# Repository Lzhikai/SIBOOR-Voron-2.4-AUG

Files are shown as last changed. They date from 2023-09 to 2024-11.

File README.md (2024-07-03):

# SIBOOR-Voron-2.4-AUG  

[1. Assembly Manual 2.4r2](#1-assembly-manual-24r2)  
 
[2. Leveling plan](#2-tap-assembly-tutorial)  
 - [TAP Assembly Tutorial](#2-tap-assembly-tutorial)
 - [Cartographer3d official website](https://docs.cartographer3d.com)
 - [Cartographer3d Assembly Tutorial](#3-cartographer3d-assembly-tutorial)  
    ---(Printed version)---  
    ---(CNC version)---  

[3. Stealthburner Assembly Tutorial](#4-stealthburner-assembly-tutorial)  
 - [Y-axis limit](#install-the-y-axis-limit-switch)  
 - [Display assembly](#display-assembly)

[4. Wiring and Inspection](#4-wiring-and-inspection)  

[5. Nevermore Installation](#5-nevermore-installation)  

[6. Networking and Configuration](#6-networking-and-configuration)  
 - [Connect to WiFi](#connect-to-wifi)
 - [SSH Tools PUTTY](#ssh-tools-putty)

[7. Connect the motherboard and EBB CAN Board](#connect-the-octopus-pro-mainboard)  

 - [Connect the Octopus Pro Mainboard](#connect-the-octopus-pro-mainboard)  

 - [Connect the EBB CAN Board](#connect-the-ebb-can-board)  

[FAQ](#faq)  

## Assembly Guide
### VORON 2.4, designed by VORON DESIGN, represents an enhanced CoreXY design featuring a stable bed and a gantry that moves vertically along the Z-axis. Notably, this design introduces added complexity, incorporating features like 4-point gantry tramming for precise alignment with the print surface, additional stepper motors, and other unique elements. Furthermore, it is crafted to operate within a fully enclosed environment, making it exceptionally proficient in printing ABS or similar filaments.
### Thank you for purchasing the V2.4 [AUG] 3D printer kit from SIBOOR. Due to version differences, please carefully read the following steps. If you encounter any issues or difficulties, please contact us promptly. Wishing you a smooth experience ahead.
### Join our Discord and WeChat groups to receive after-sales support.

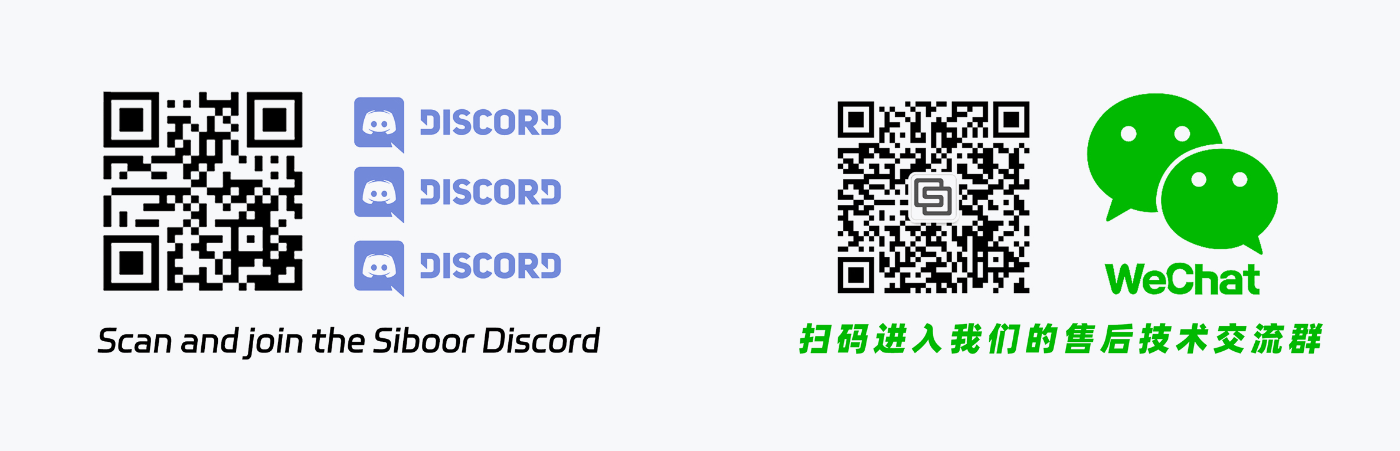
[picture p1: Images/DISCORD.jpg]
 <br/><br/>  

### Please read in the order presented on this page.

### 1. Assembly Manual 2.4r2

- [Assembly_Manual 2.4r2 SIBOOR Annotation Version.pdf](https://github.com/Lzhikai/SIBOOR-Voron-2.4-AUG/blob/main/Manual/Assembly_Manual_2.4r2%EF%BC%88SIBOOR%20Annotation%20Version%EF%BC%89.pdf)  
- Pay close attention to manual comments. After downloading, open the file using a browser or PDF software to view the annotation content!  
- Green-highlighted sections denote variances between SIBOOR V2.4 [AUG] and VORON's official BOM.  
- Red-highlighted sections indicate differences in metal structural components between SIBOOR V2.4 [AUG] and VORON's official BOM.  
  
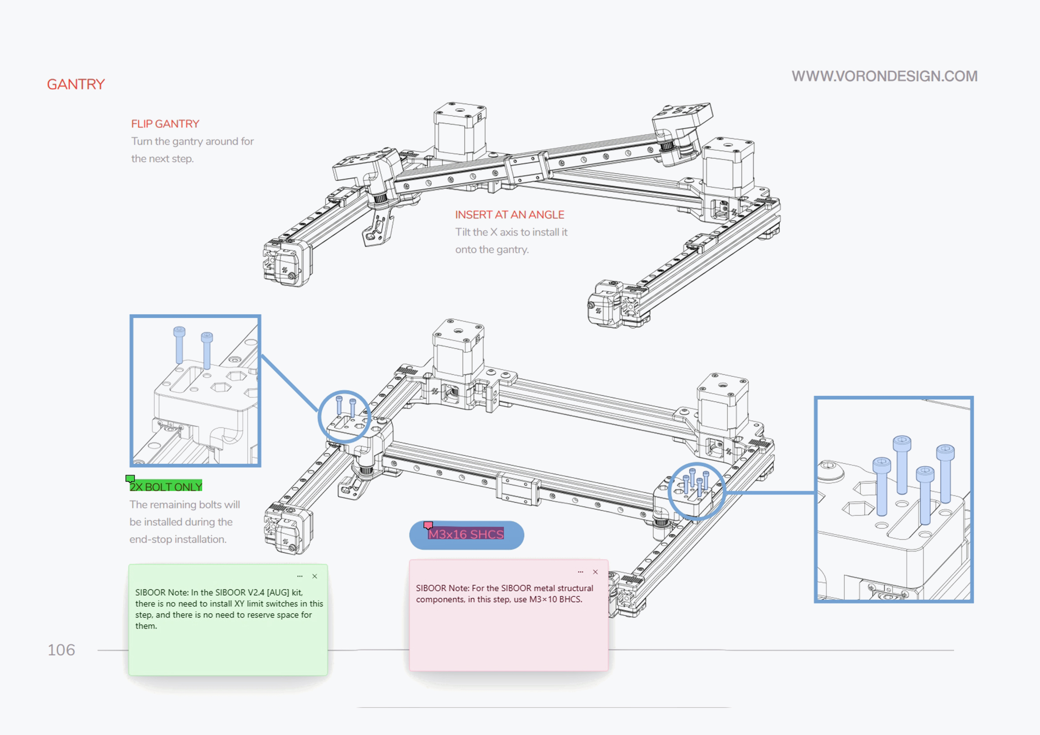
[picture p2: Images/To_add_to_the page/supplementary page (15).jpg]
  

### 2. TAP Assembly Tutorial  

- [Assembly_Manual_Tap.pdf](https://github.com/Lzhikai/SIBOOR-Voron-2.4-AUG/blob/main/Manual/Assembly_Manual_Tap.pdf)  

- Currently, TAP has been upgraded to the RCB version. See the differences in assembly with the old version in the following images.  
  
- **Belt handling:**
  The belts are now handled by looping around Tap_center, and secured with a printed belt cover and M3x8 BHCS:  
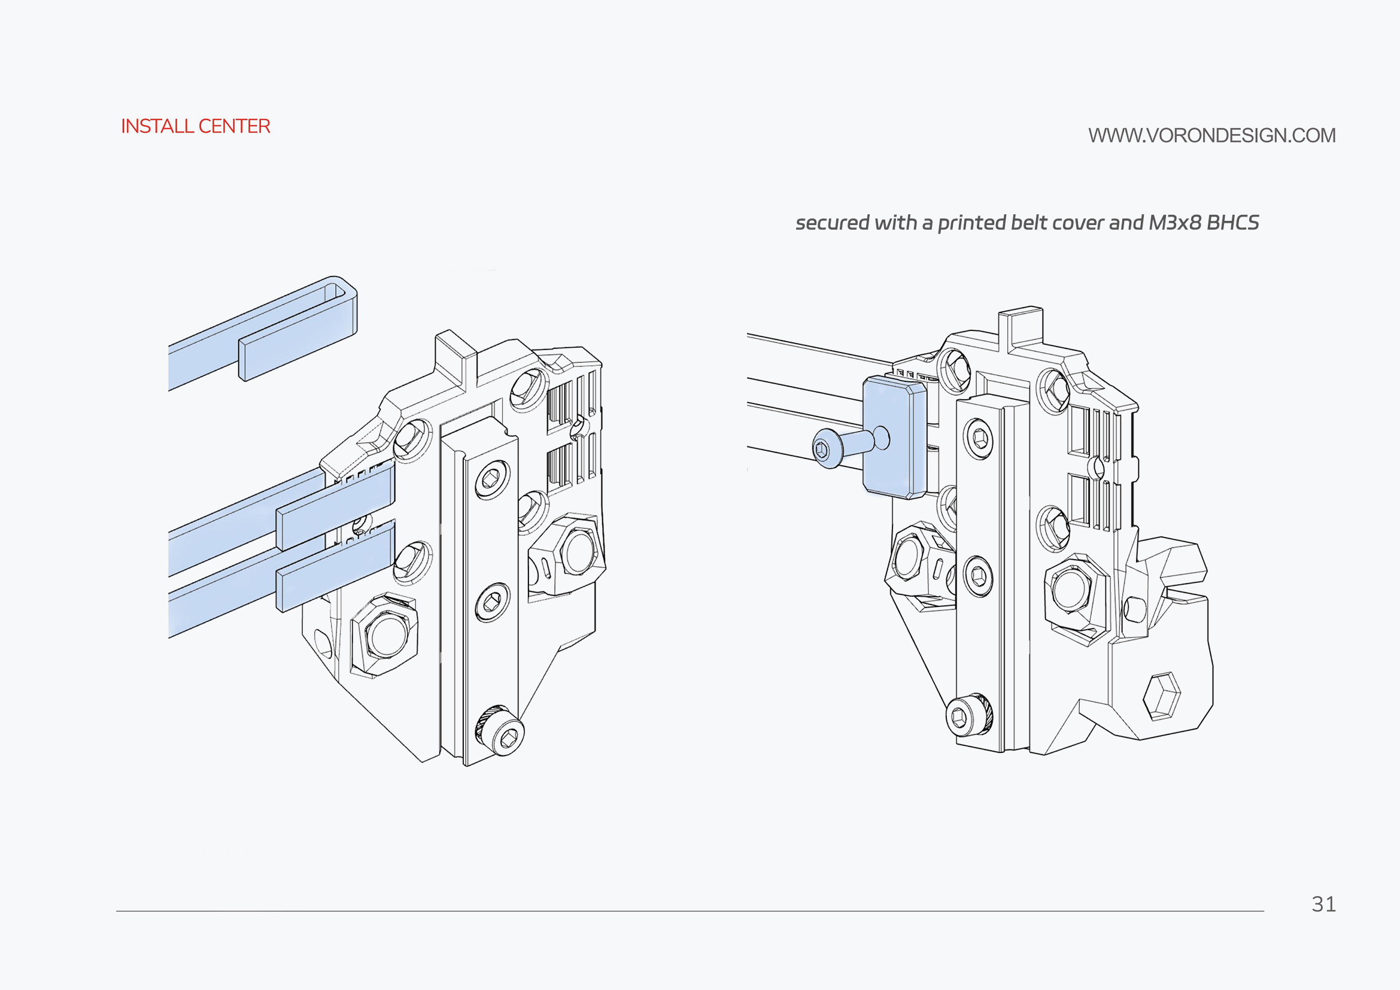
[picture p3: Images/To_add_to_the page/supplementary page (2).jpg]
    

- **Extra Stiffening:**
  The 2 M3x50 bolts are threaded up into Tap_Center, and serve to provide extra stiffening:  
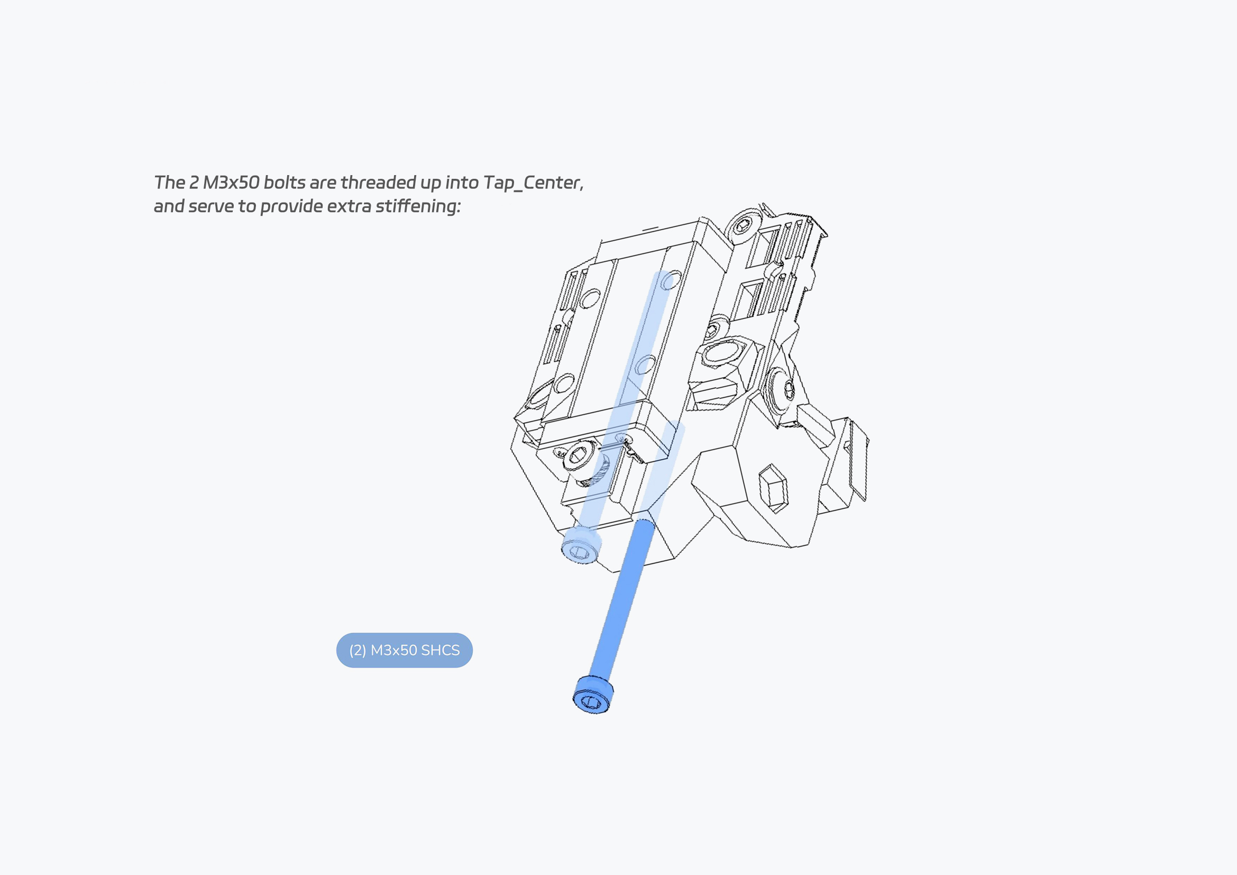
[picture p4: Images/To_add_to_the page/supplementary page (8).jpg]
    

- **Vibration Resistance:**
  The heatset inserts for the center are moved back 4 mm to provide extra vibration resistance:  
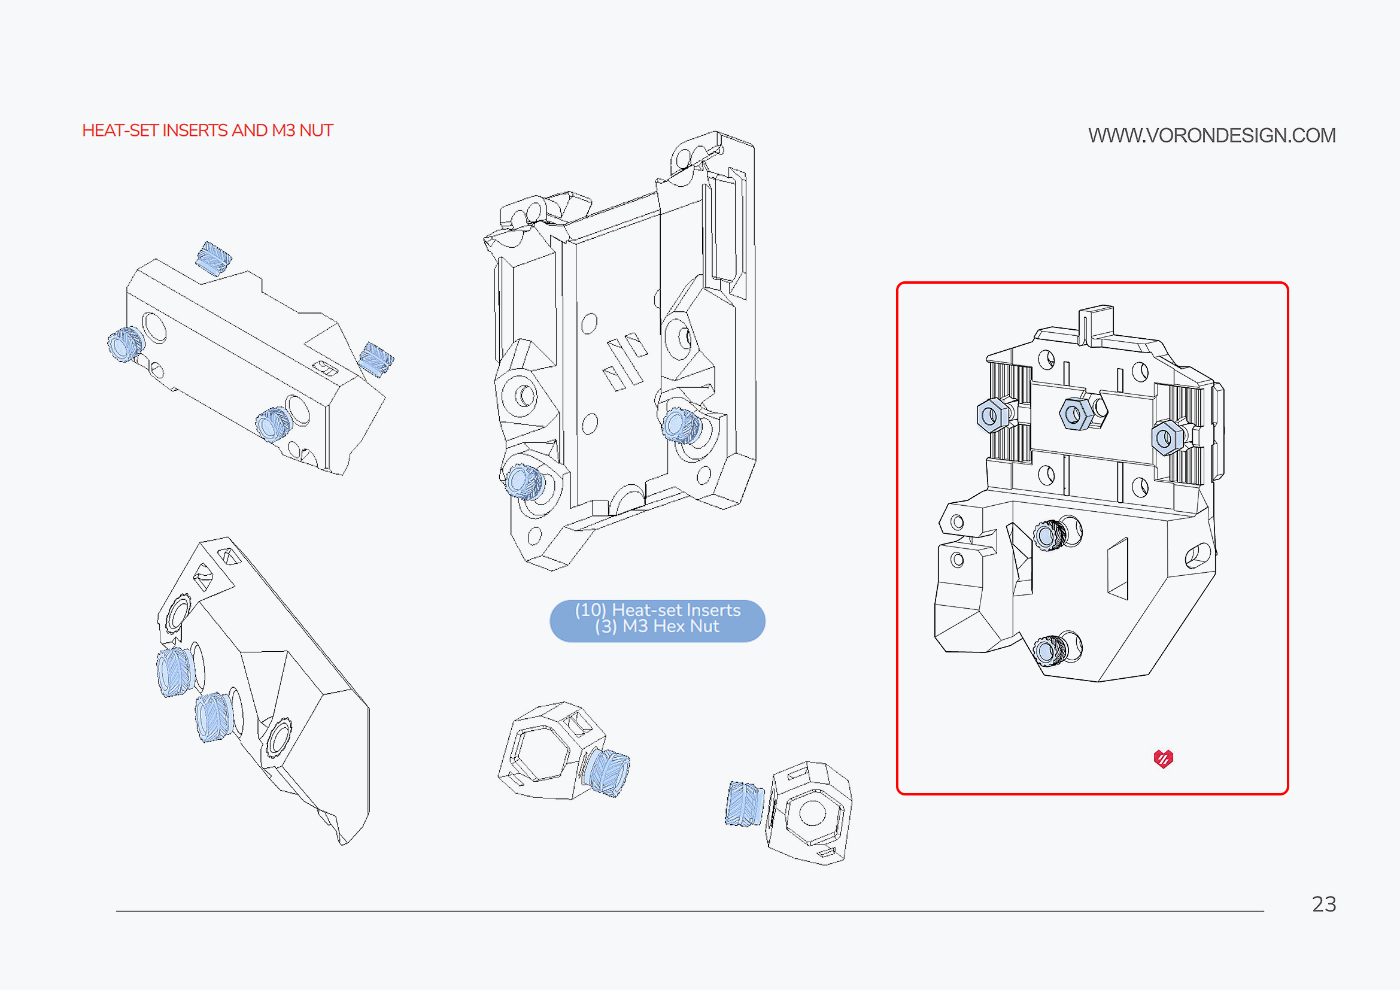
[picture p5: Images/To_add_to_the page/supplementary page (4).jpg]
    

- **Secure with Screws:**
  So they will need to be secured with M3x12 and M3x16 SHCS (The top is still secured by M3x6 SHCS):  
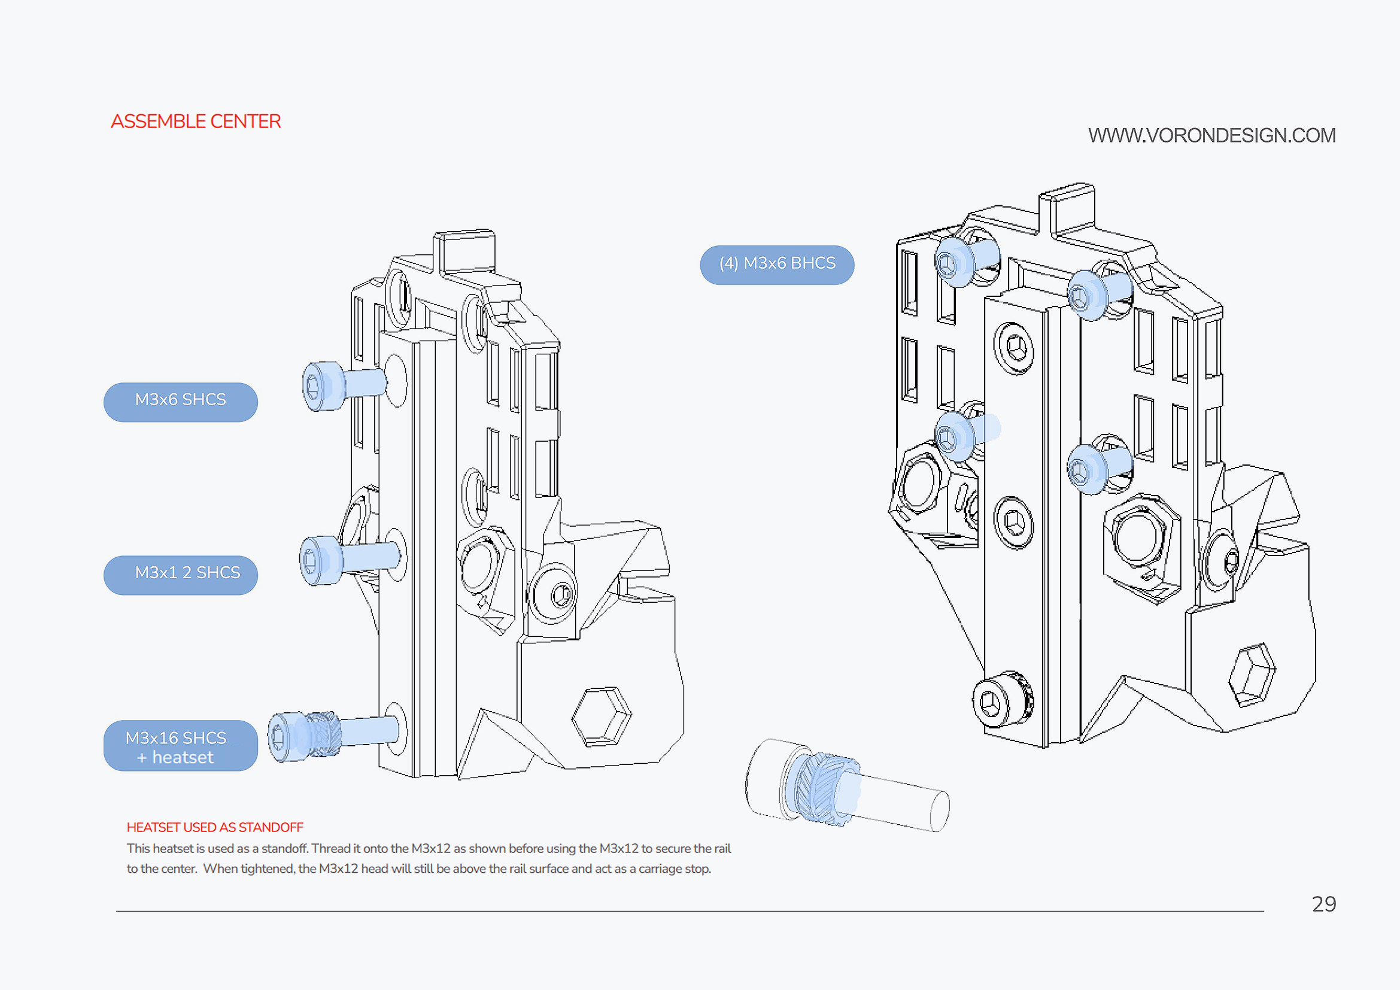
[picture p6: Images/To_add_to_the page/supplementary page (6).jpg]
    

- After completing the TAP module, go directly to page 132 of the "Assembly_Manual 2.4r2 SIBOOR Annotation Version.pdf.  

### 3. Cartographer3d Assembly Tutorial  
- ### Printed version
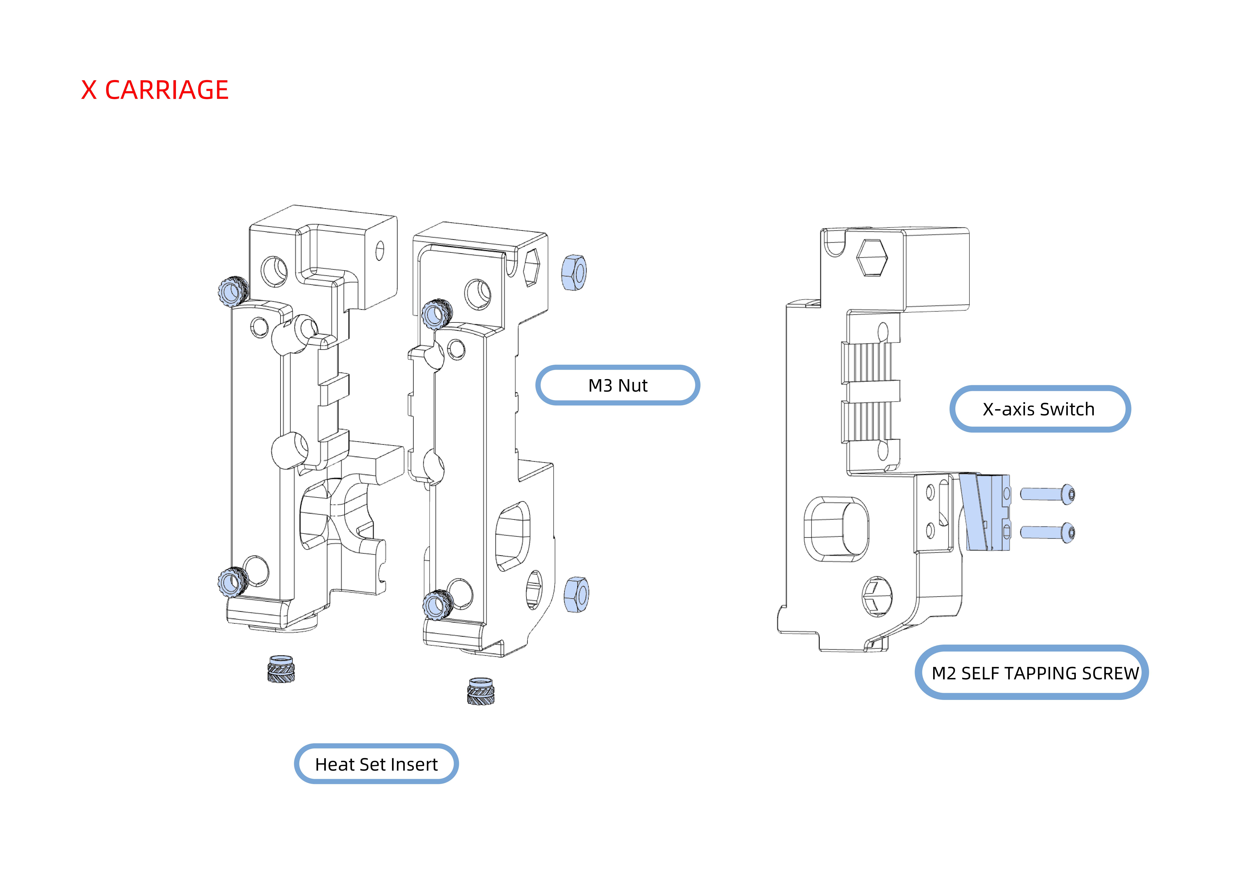
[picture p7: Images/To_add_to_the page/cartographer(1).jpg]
    
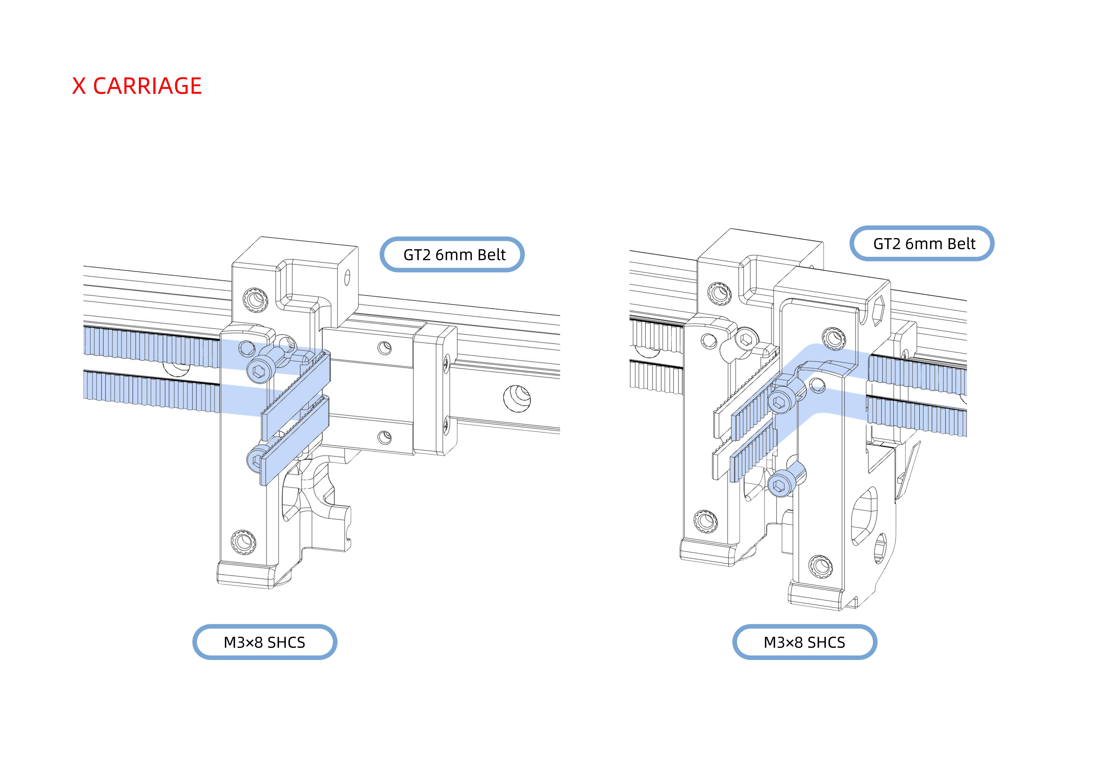
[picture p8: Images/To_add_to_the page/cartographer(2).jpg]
    
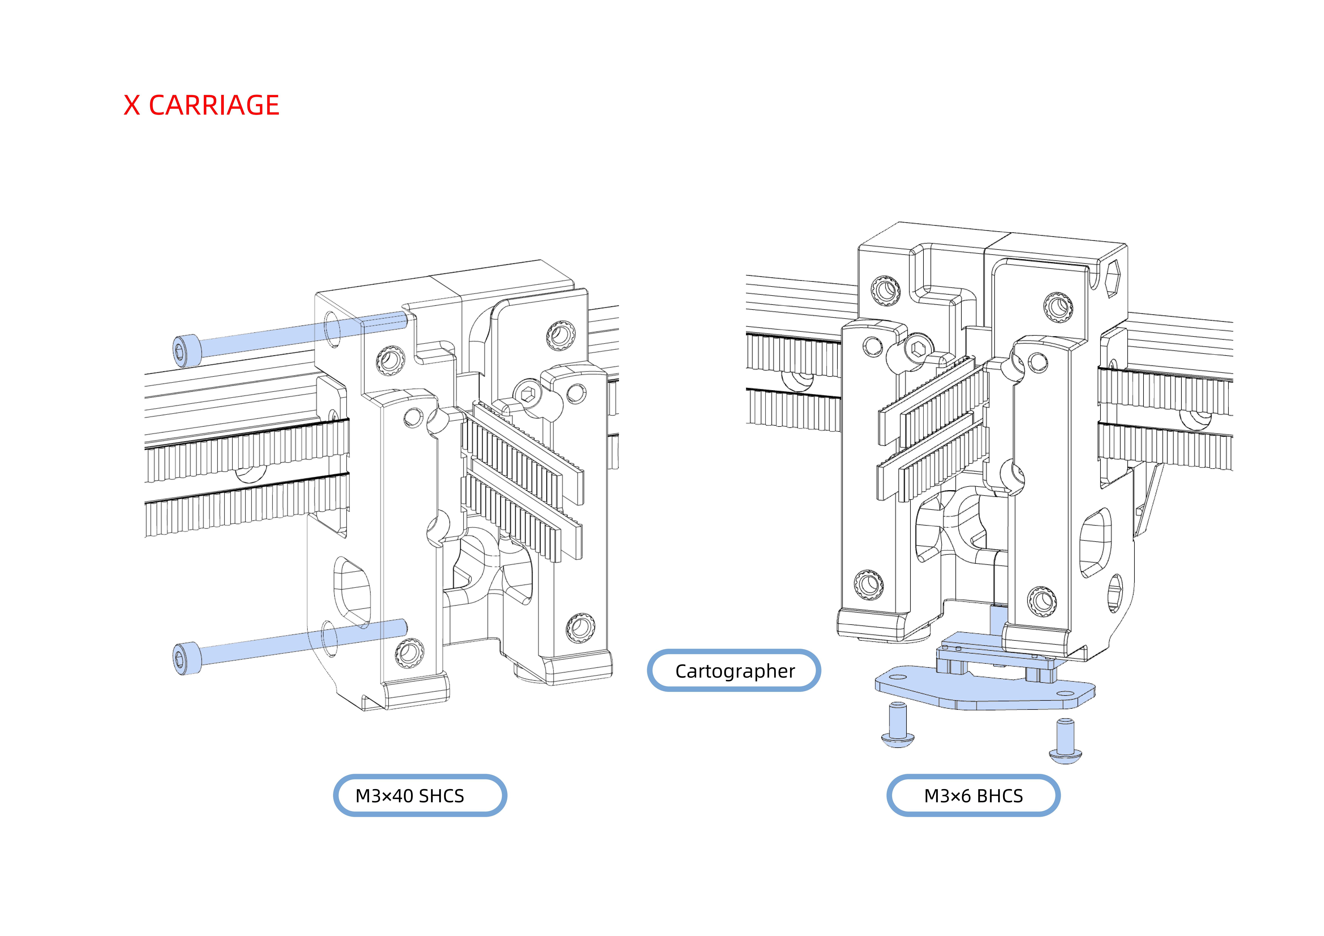
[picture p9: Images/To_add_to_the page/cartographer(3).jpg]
  
- ### CNC version
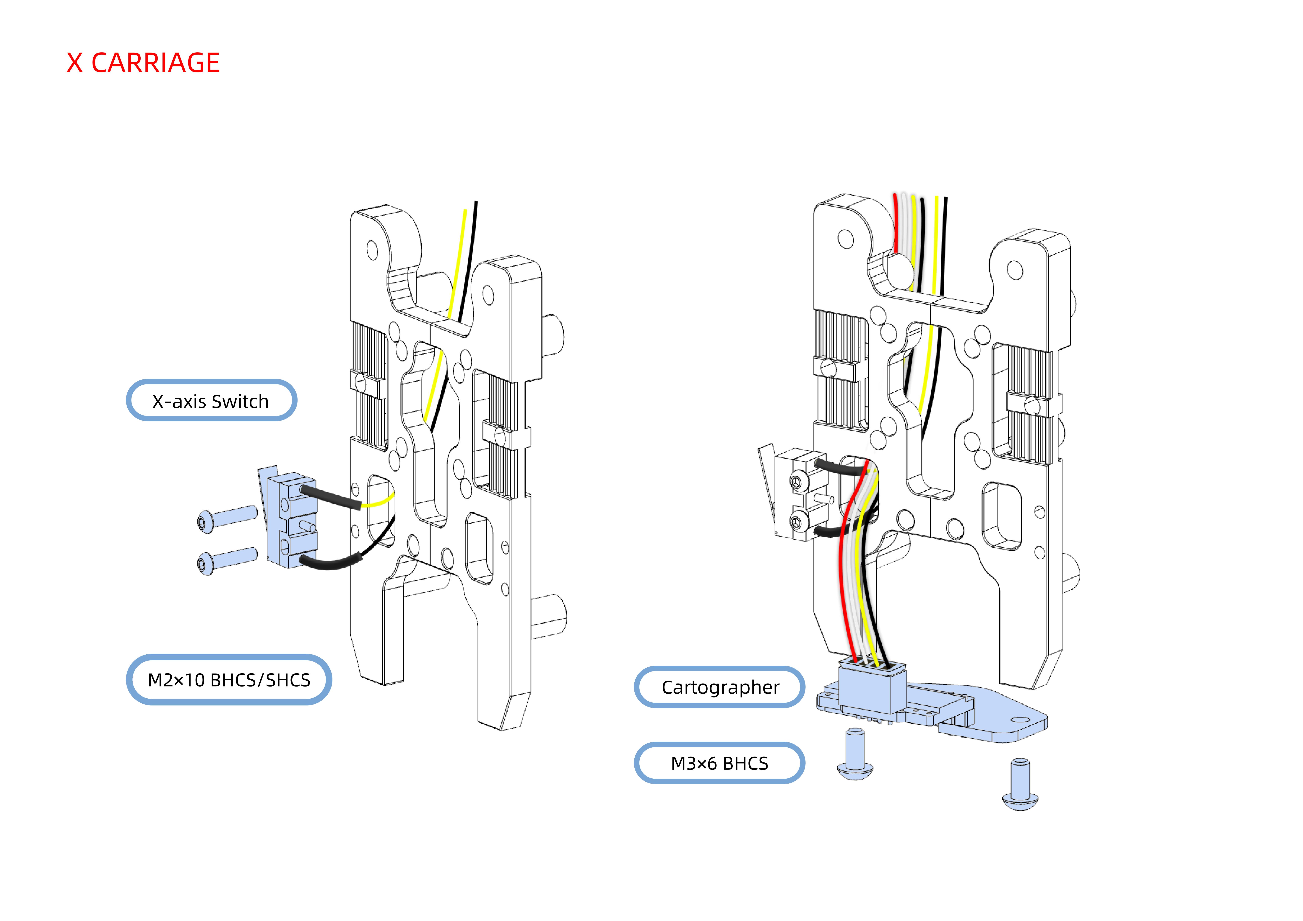
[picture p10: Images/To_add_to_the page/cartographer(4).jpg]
    
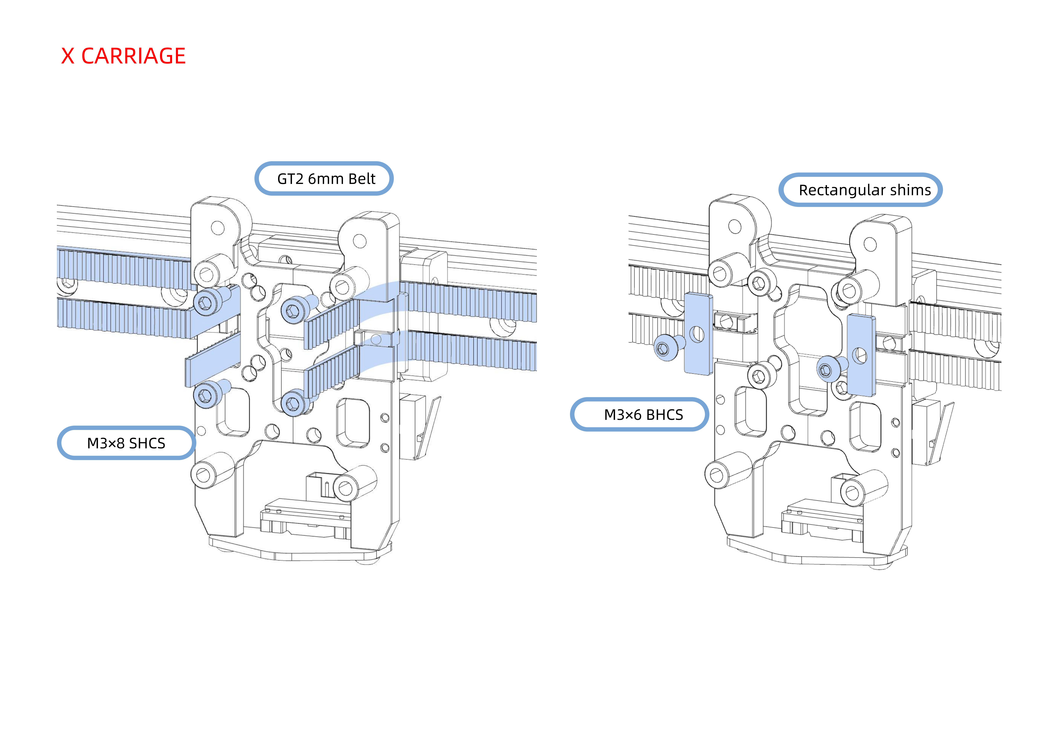
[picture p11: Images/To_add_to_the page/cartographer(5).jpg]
    
  
### 4. Stealthburner Assembly Tutorial  

- Install the heating rod and thermistor.  
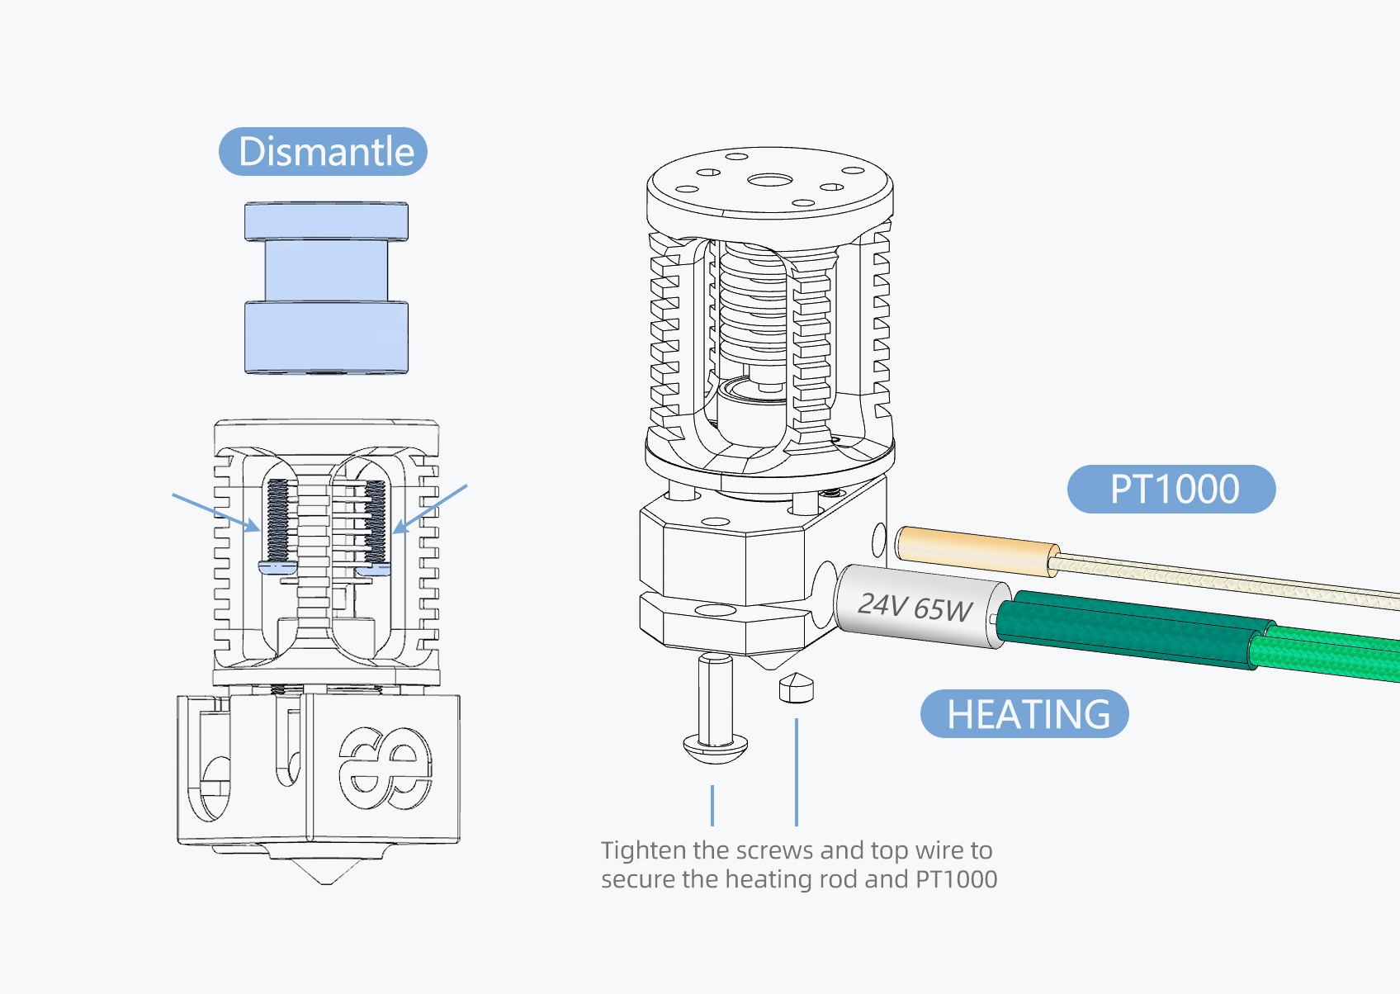
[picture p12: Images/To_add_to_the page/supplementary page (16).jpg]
    

- [Assembly_Manual_Stealthburner.pdf](https://github.com/Lzhikai/SIBOOR-Voron-2.4-AUG/blob/main/Manual/Assembly_Manual_SB%EF%BC%88SIBOOR%20Annotation%20Version%EF%BC%89.pdf)  

- Set up the CAN board, illustrate wiring, and set jumpers.  
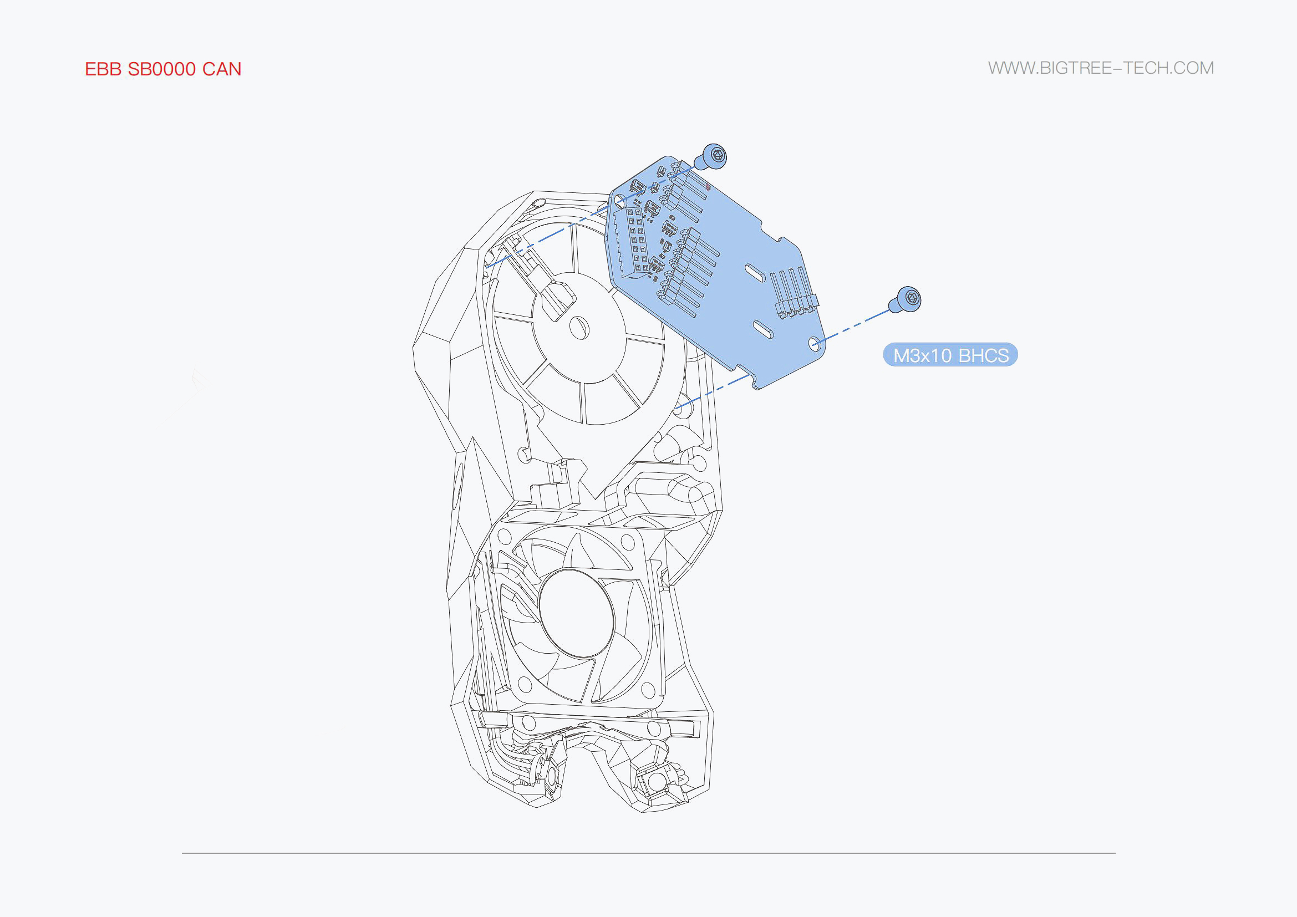
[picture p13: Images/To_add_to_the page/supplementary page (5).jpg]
    
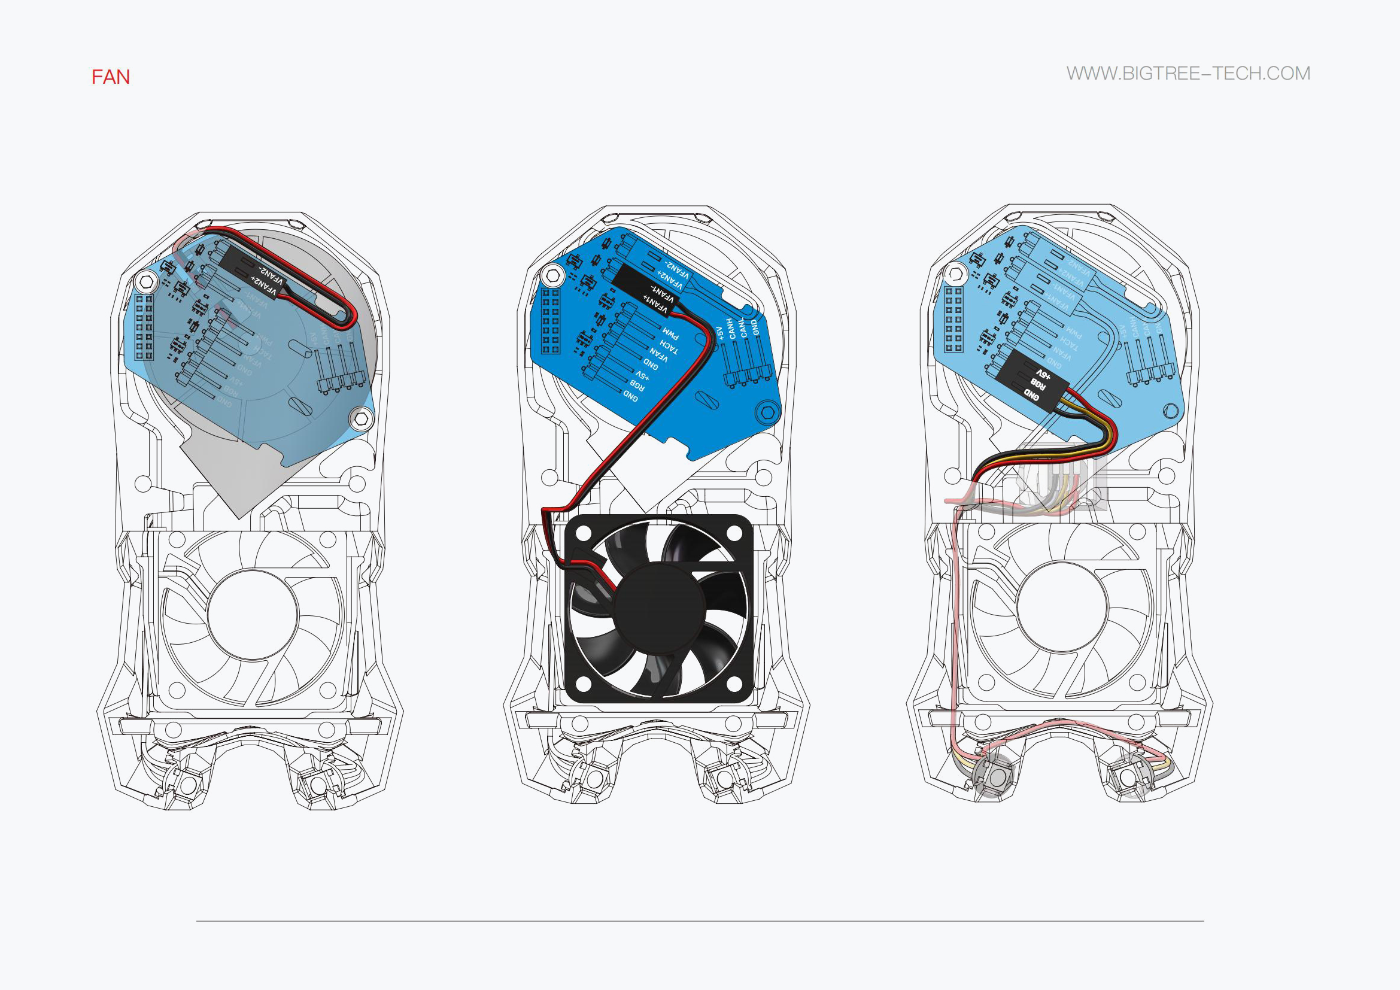
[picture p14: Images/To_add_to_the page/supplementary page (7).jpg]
    
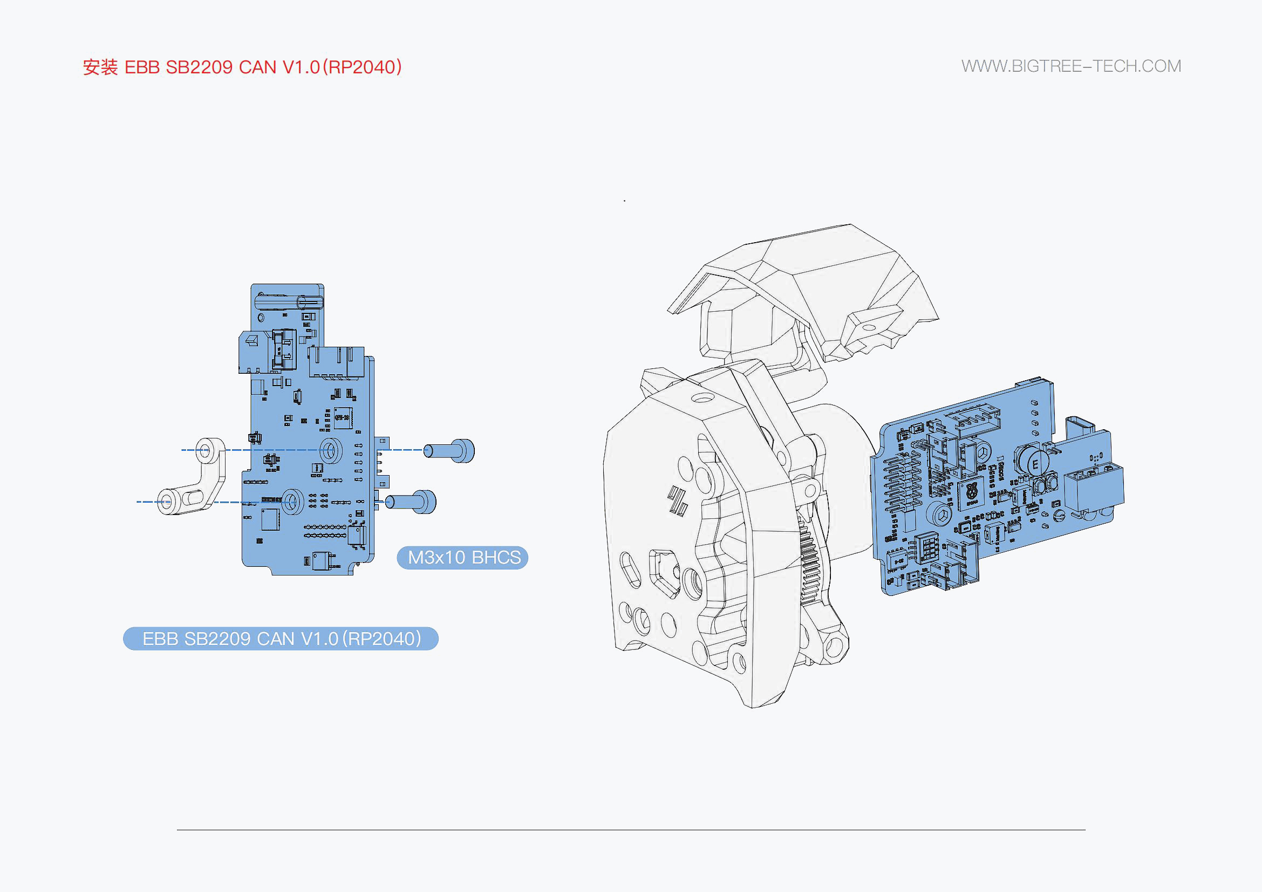
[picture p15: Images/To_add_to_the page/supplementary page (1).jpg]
    
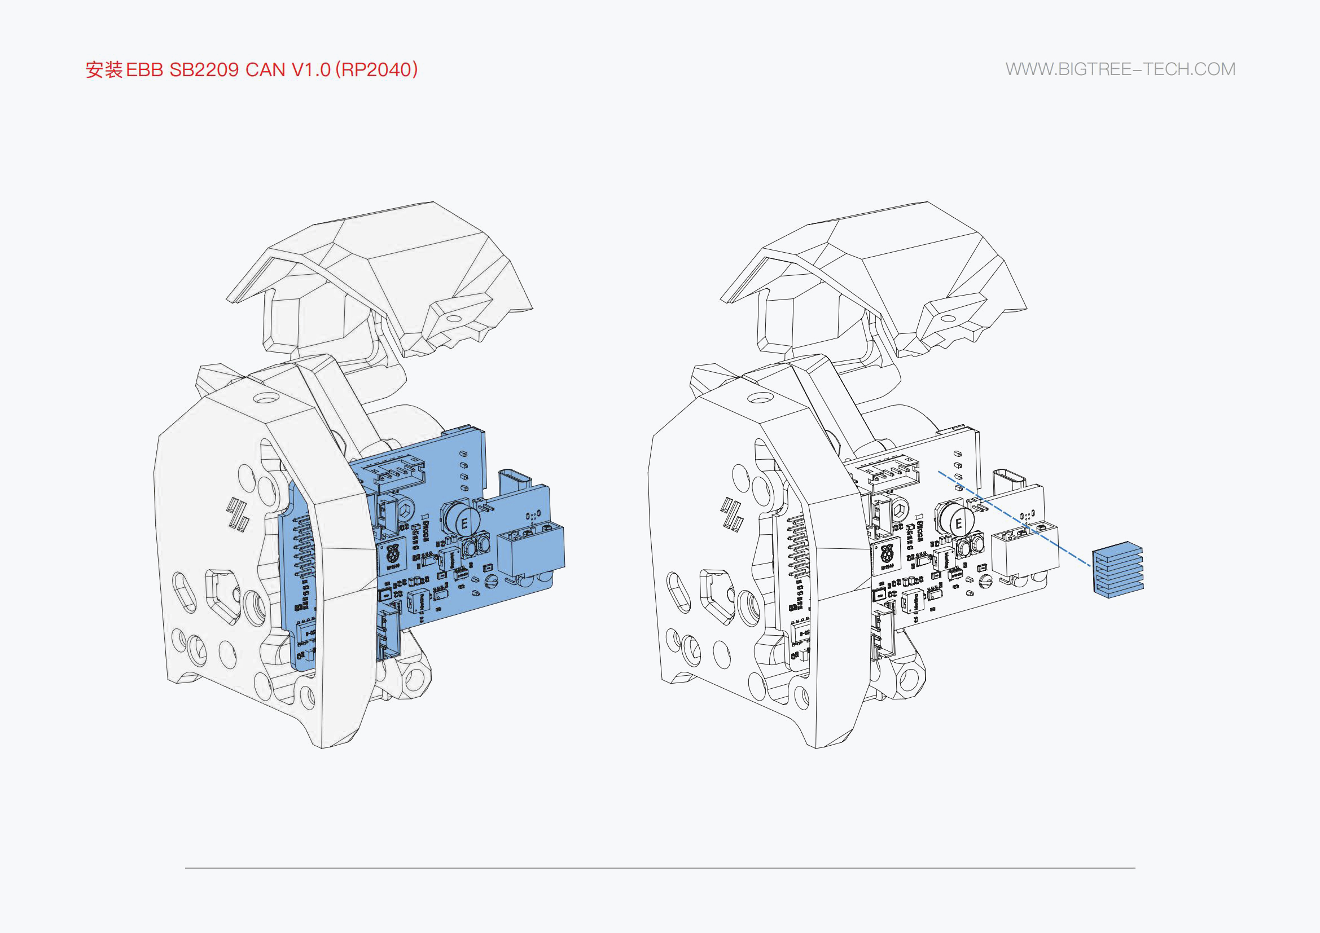
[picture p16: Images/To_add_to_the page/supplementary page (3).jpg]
    
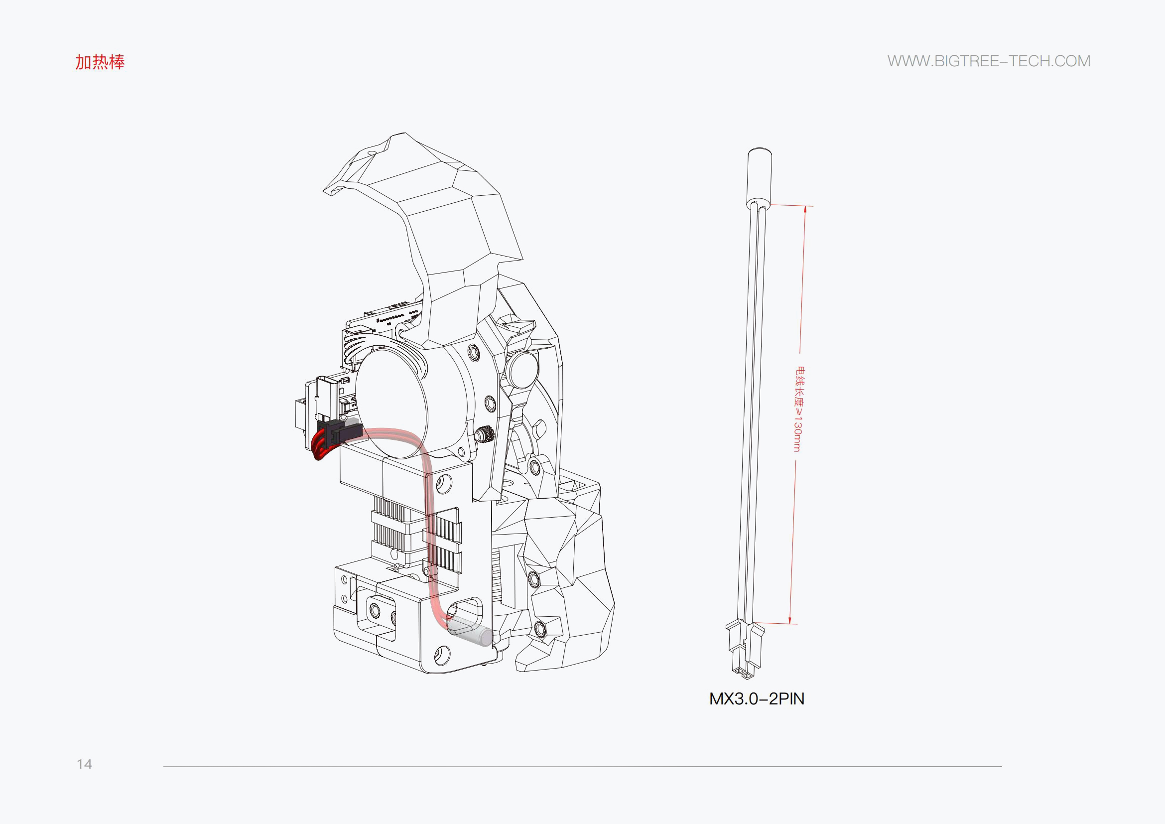
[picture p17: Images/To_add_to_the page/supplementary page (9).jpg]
    
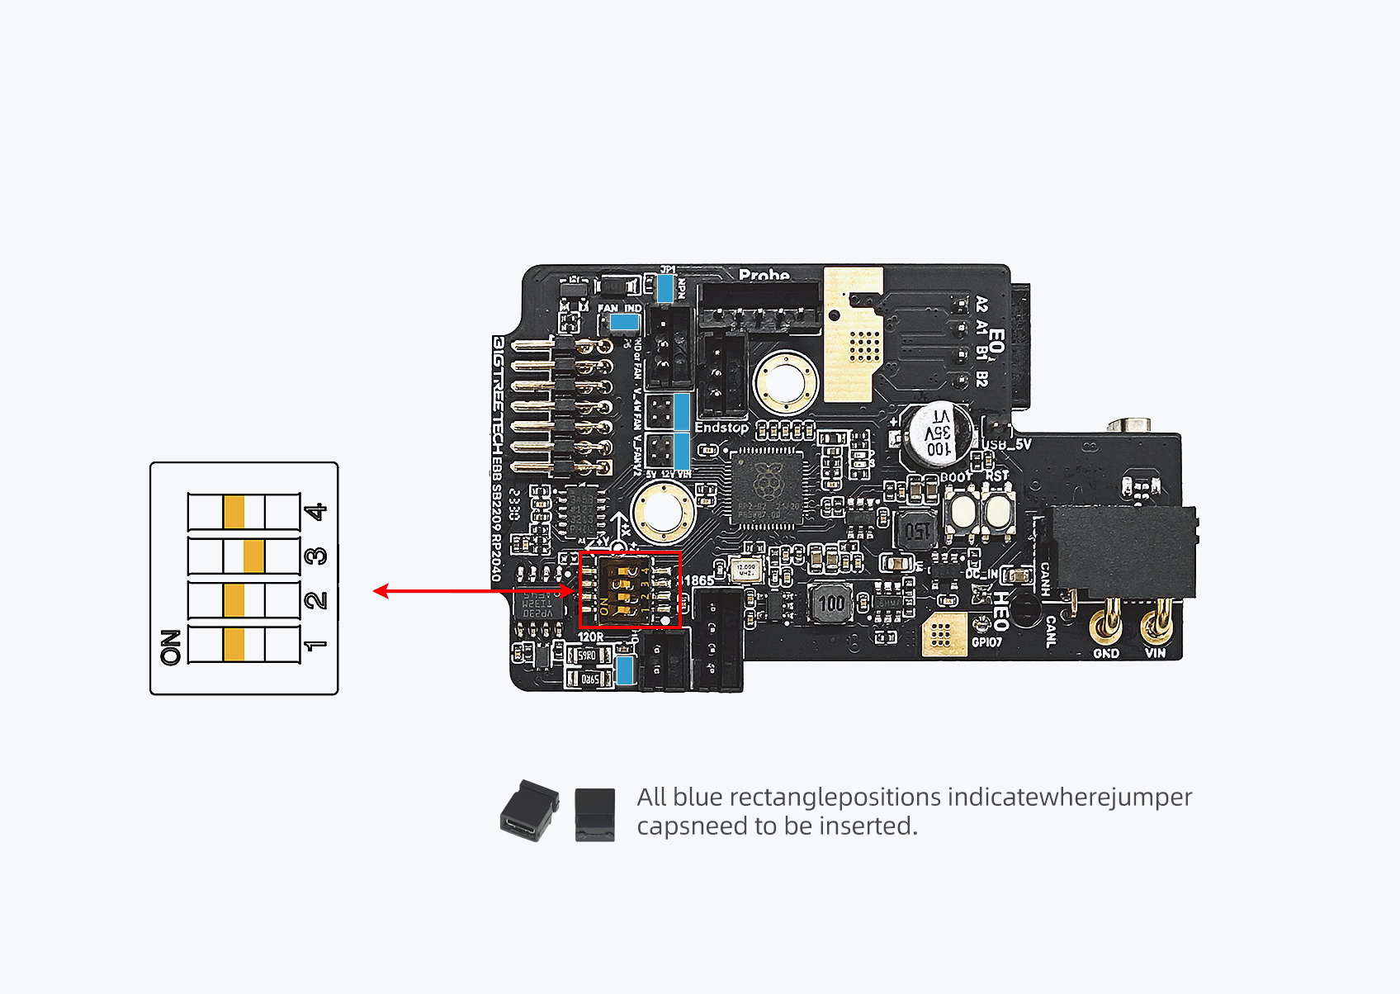
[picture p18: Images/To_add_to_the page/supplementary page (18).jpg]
    
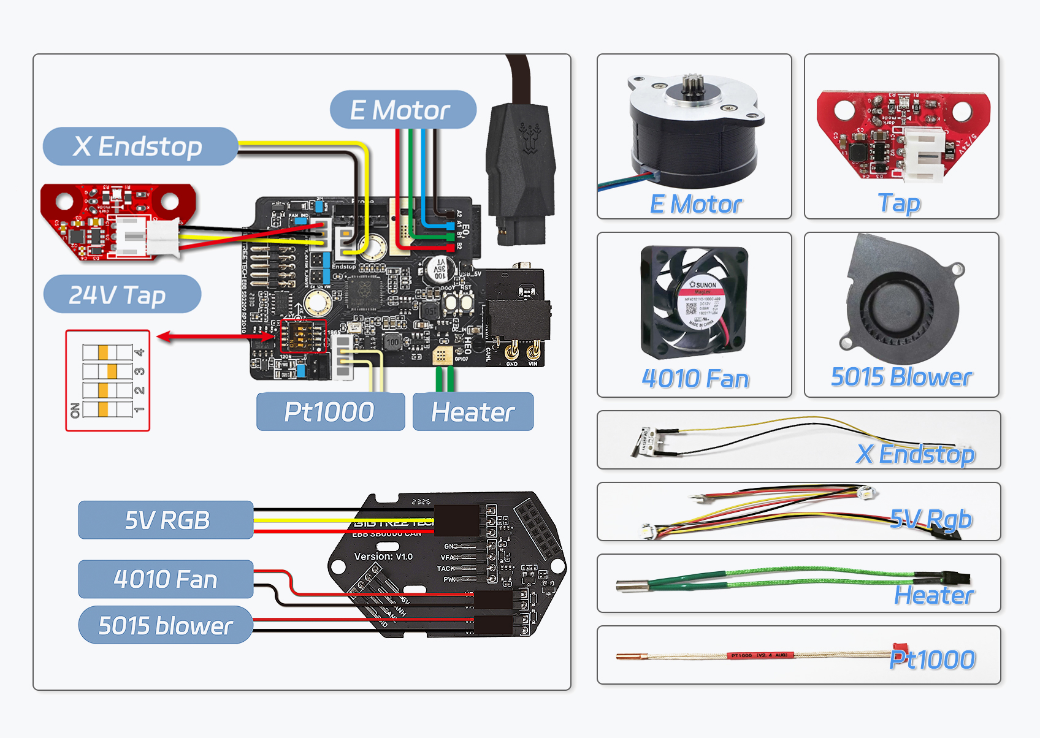
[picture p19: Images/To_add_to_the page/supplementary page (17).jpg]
    
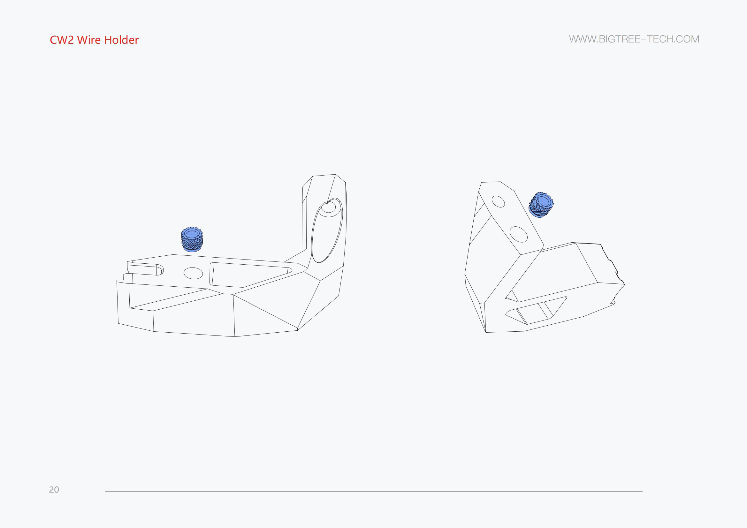
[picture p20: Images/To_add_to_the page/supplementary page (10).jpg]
    
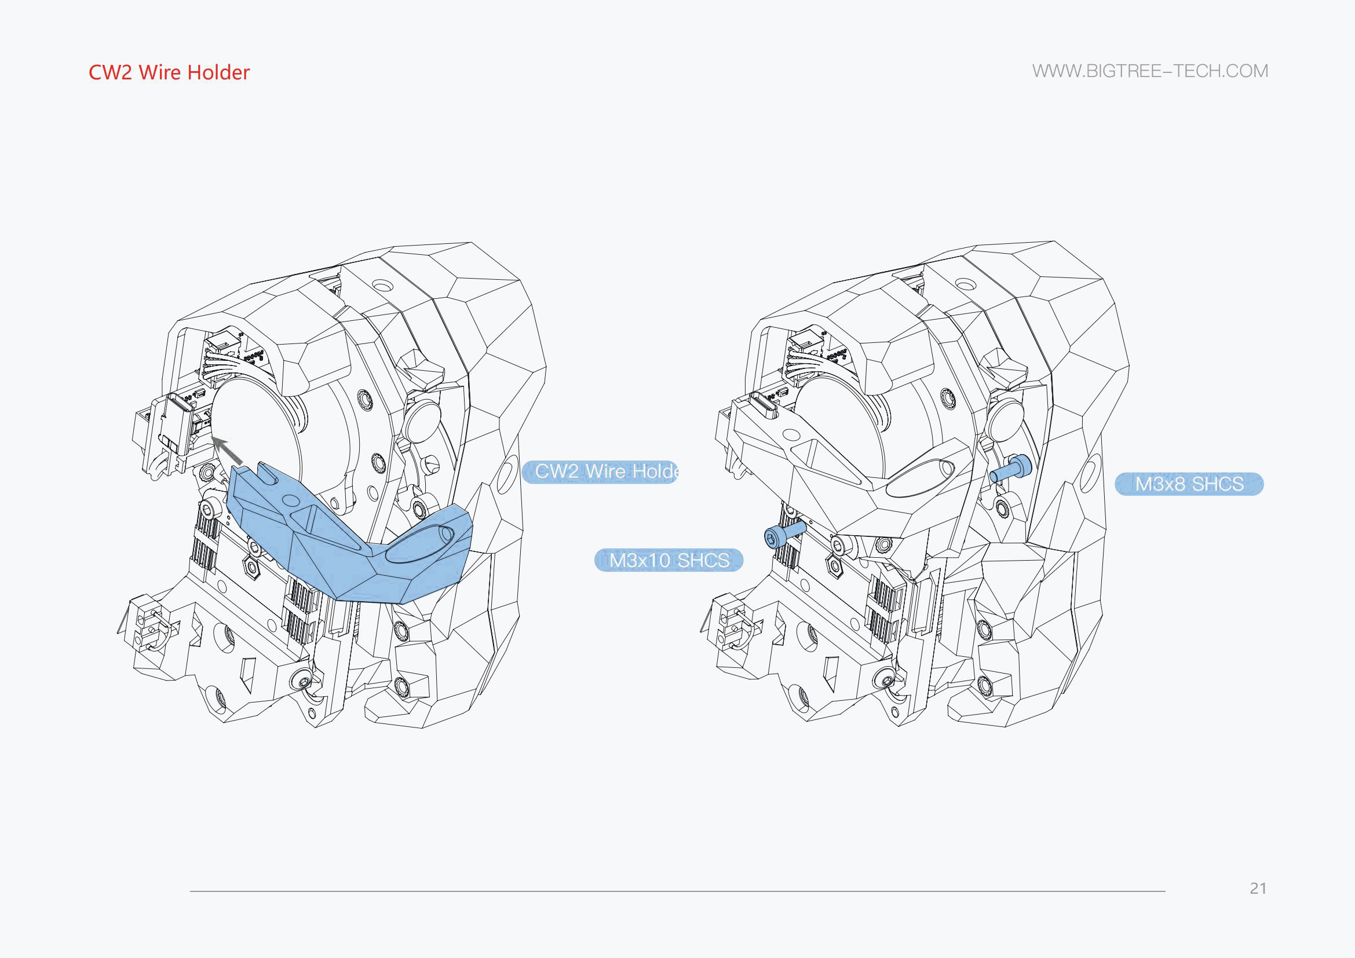
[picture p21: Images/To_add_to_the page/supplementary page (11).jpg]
    
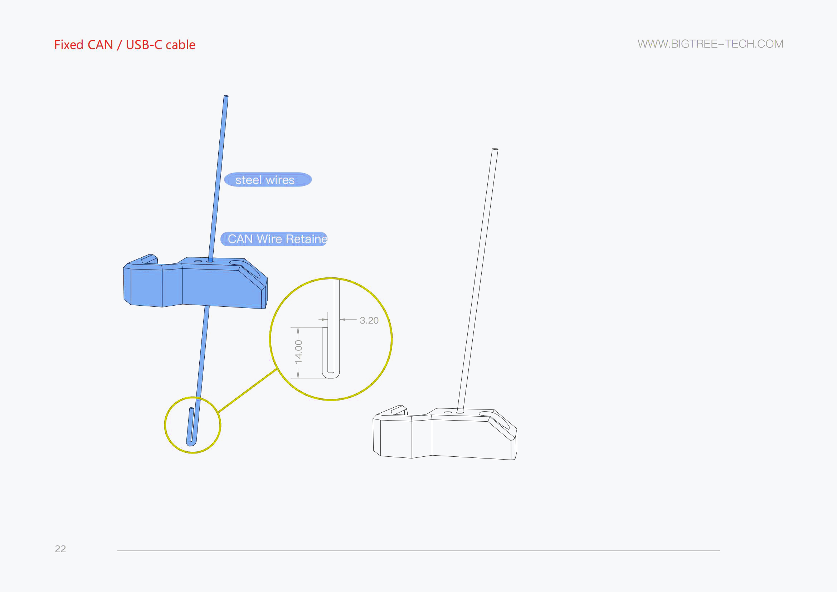
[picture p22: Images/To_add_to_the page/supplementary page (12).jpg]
  
  
### Display-Assembly  
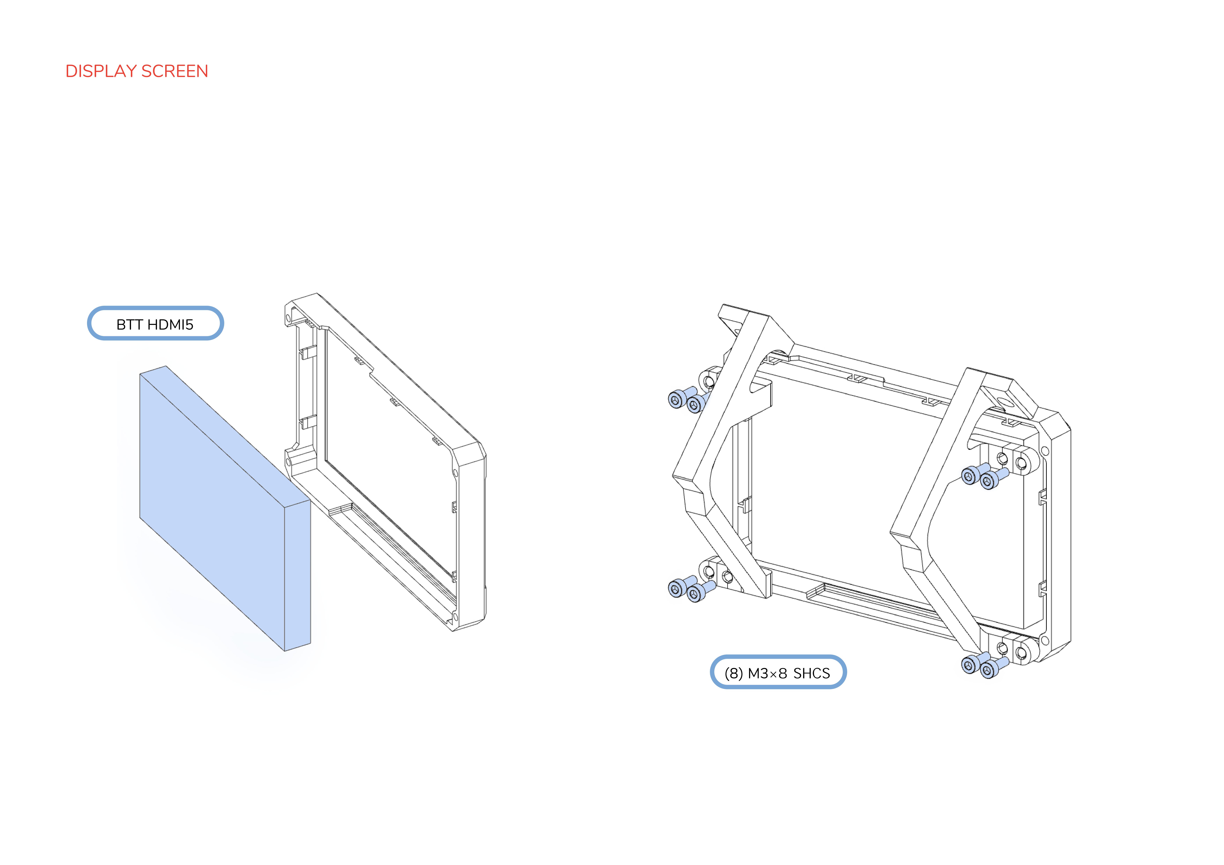
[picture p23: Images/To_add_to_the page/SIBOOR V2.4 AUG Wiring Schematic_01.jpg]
    
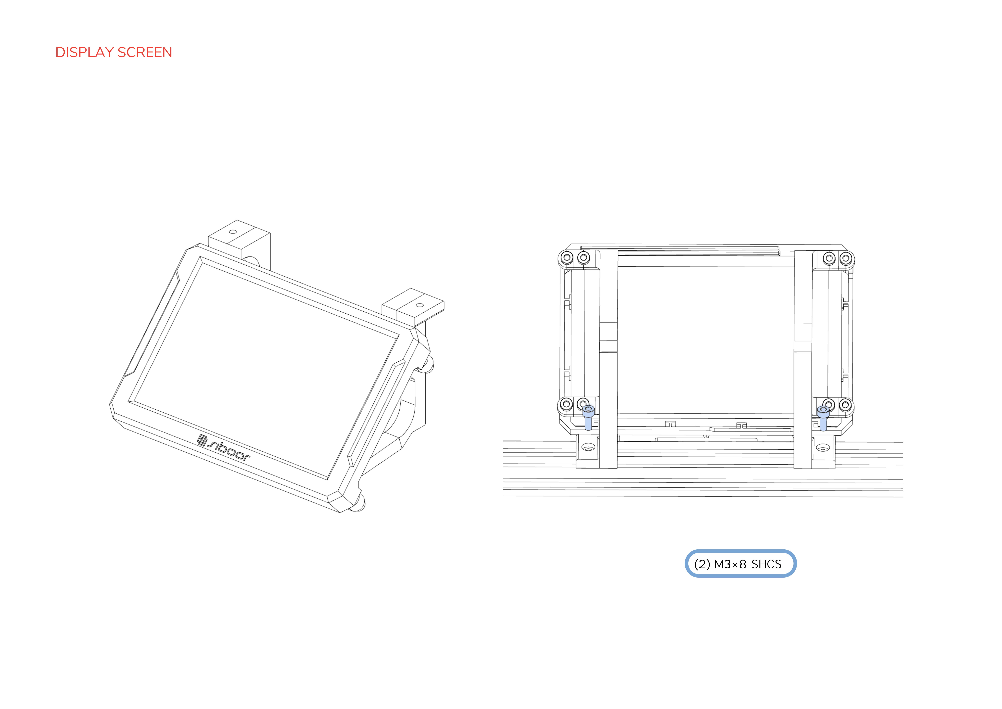
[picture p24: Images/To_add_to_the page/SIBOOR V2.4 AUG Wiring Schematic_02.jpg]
  

### Install the Y-axis limit switch   
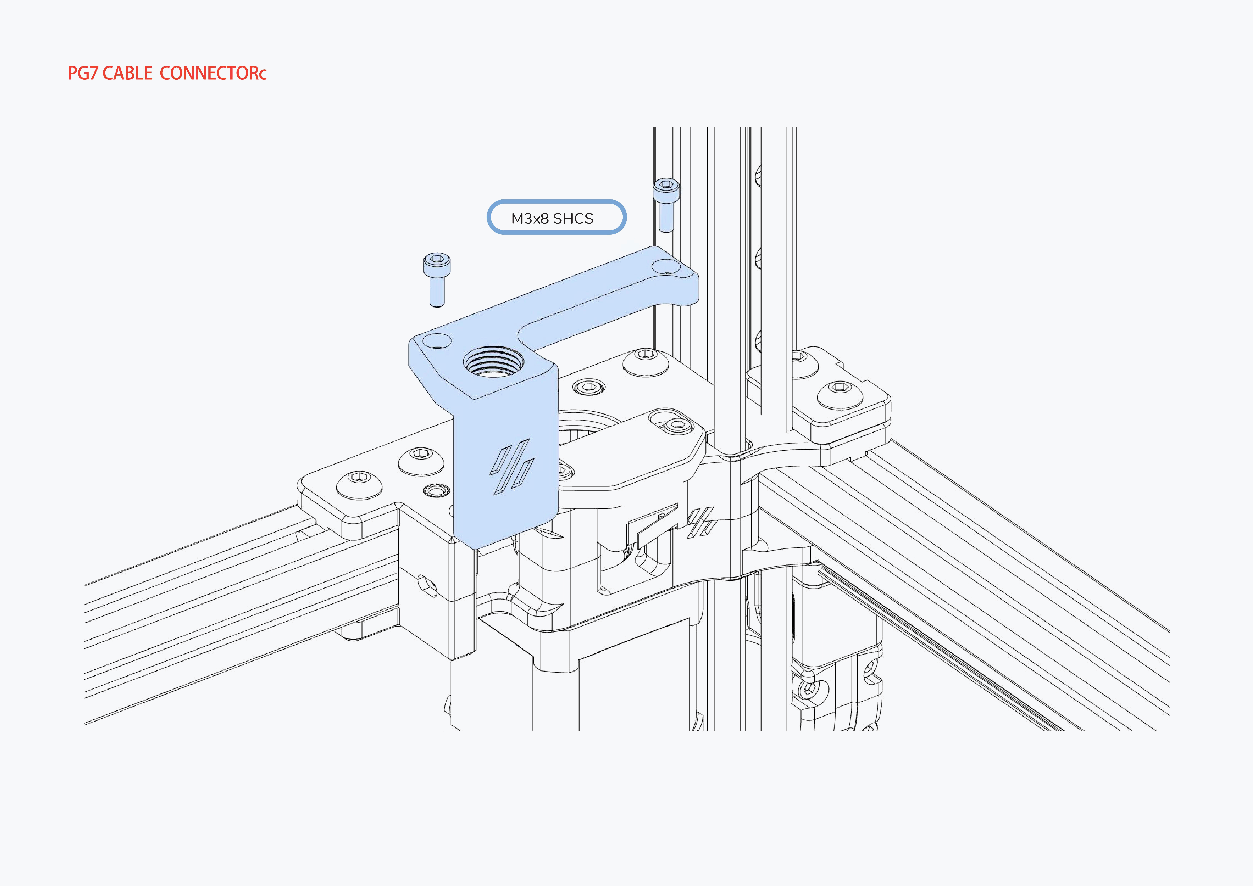
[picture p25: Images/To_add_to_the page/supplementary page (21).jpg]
    
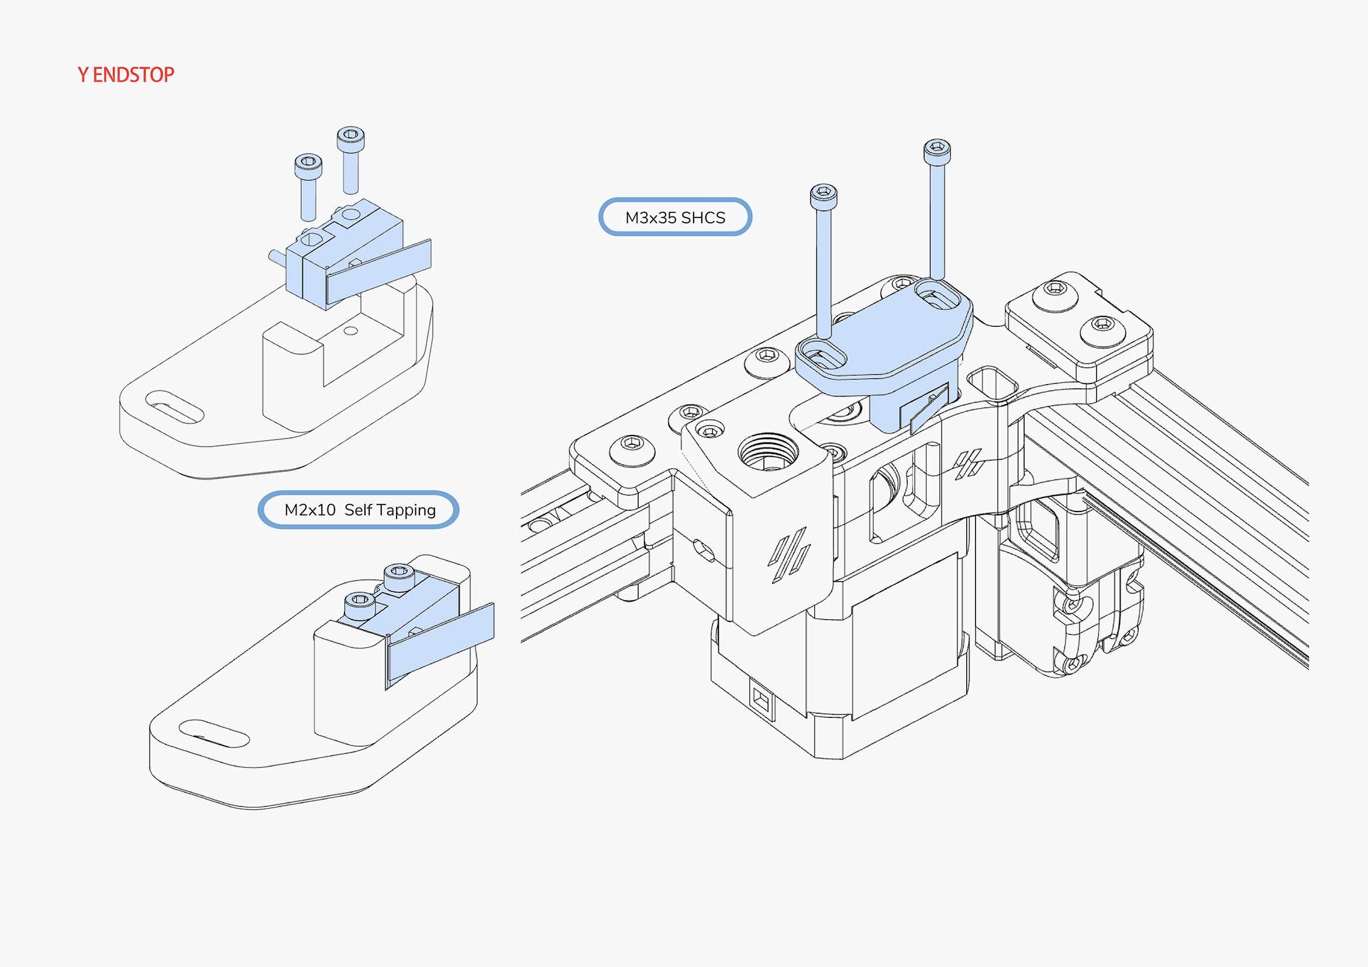
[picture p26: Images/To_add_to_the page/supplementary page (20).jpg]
    

- Install CAN board cables and steel wires.  
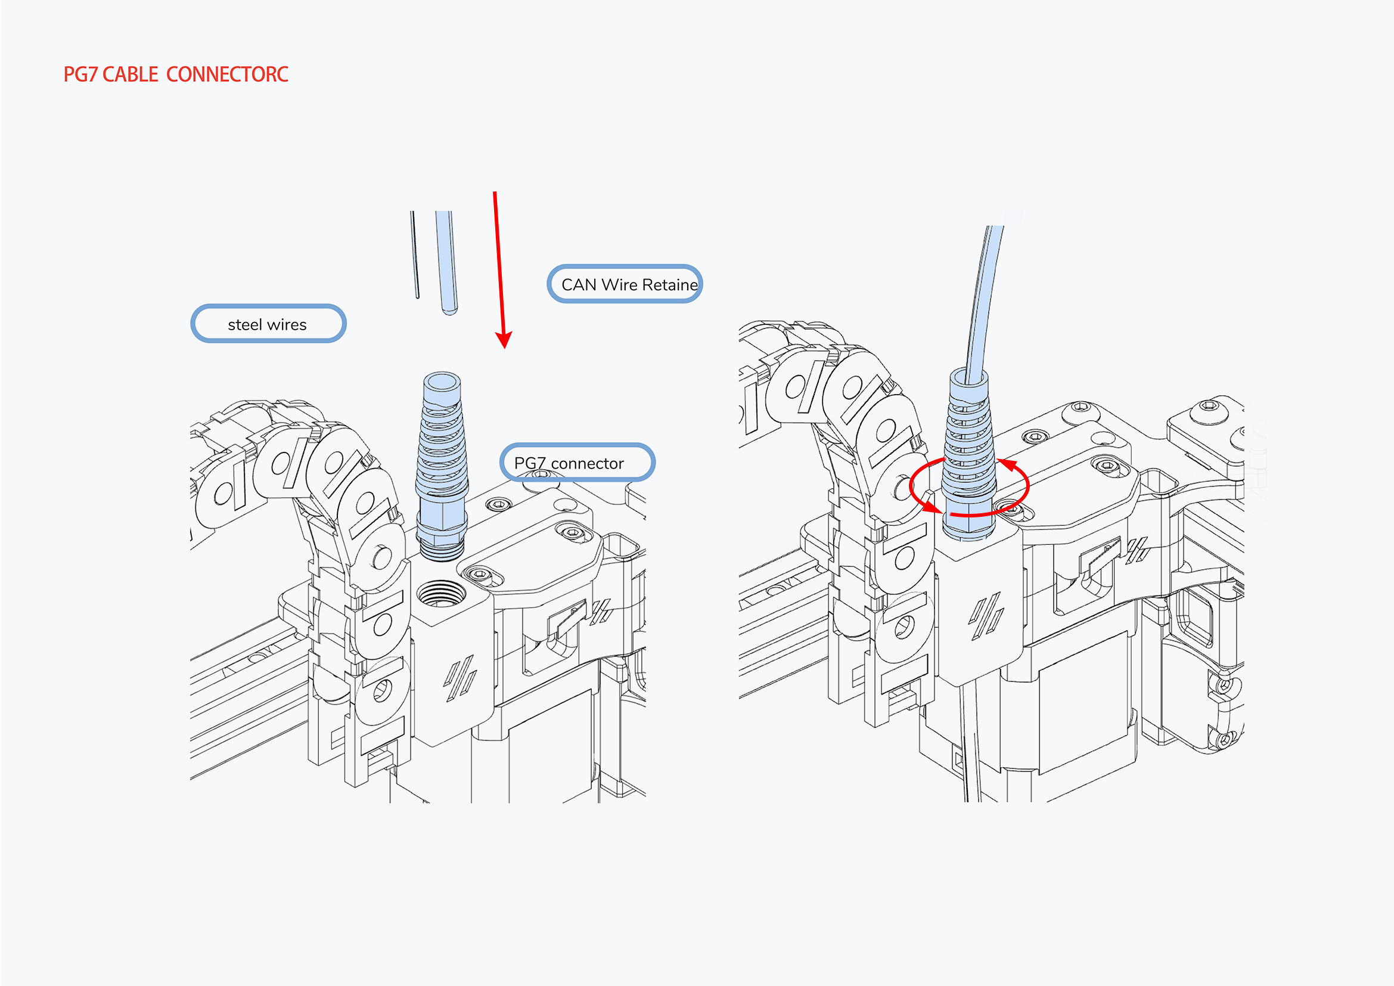
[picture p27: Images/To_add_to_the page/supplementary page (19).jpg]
    

### 4. Wiring and Inspection  

- Versions shipped by December 13, 2023  
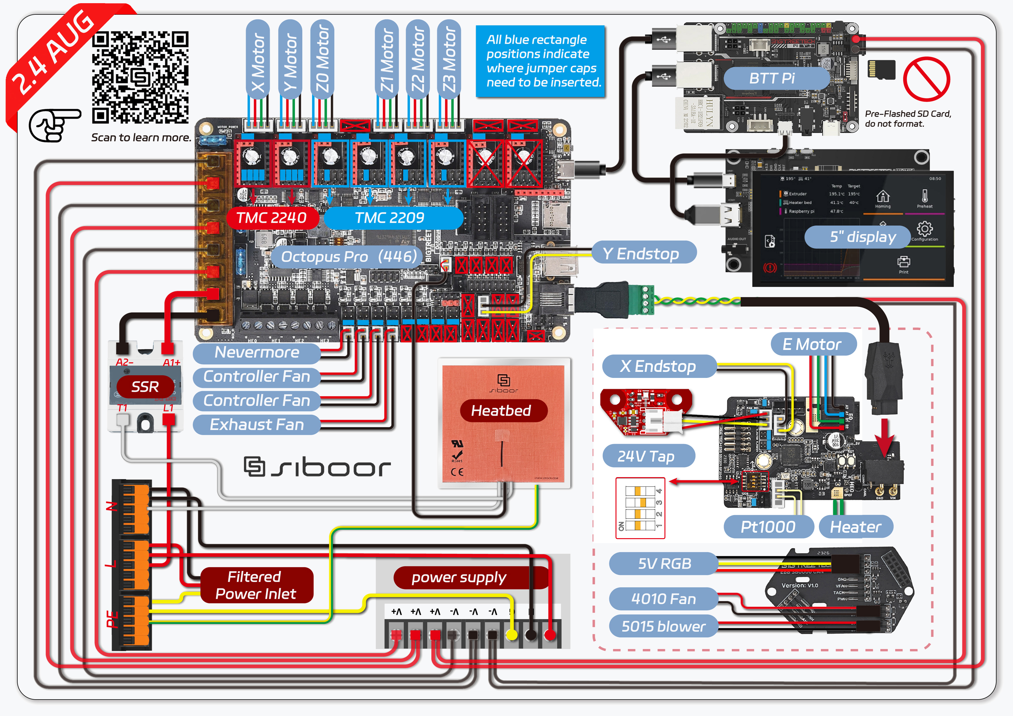
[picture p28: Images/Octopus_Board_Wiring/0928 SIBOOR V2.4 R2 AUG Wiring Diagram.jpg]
    

- Versions shipped after December 13, 2023  
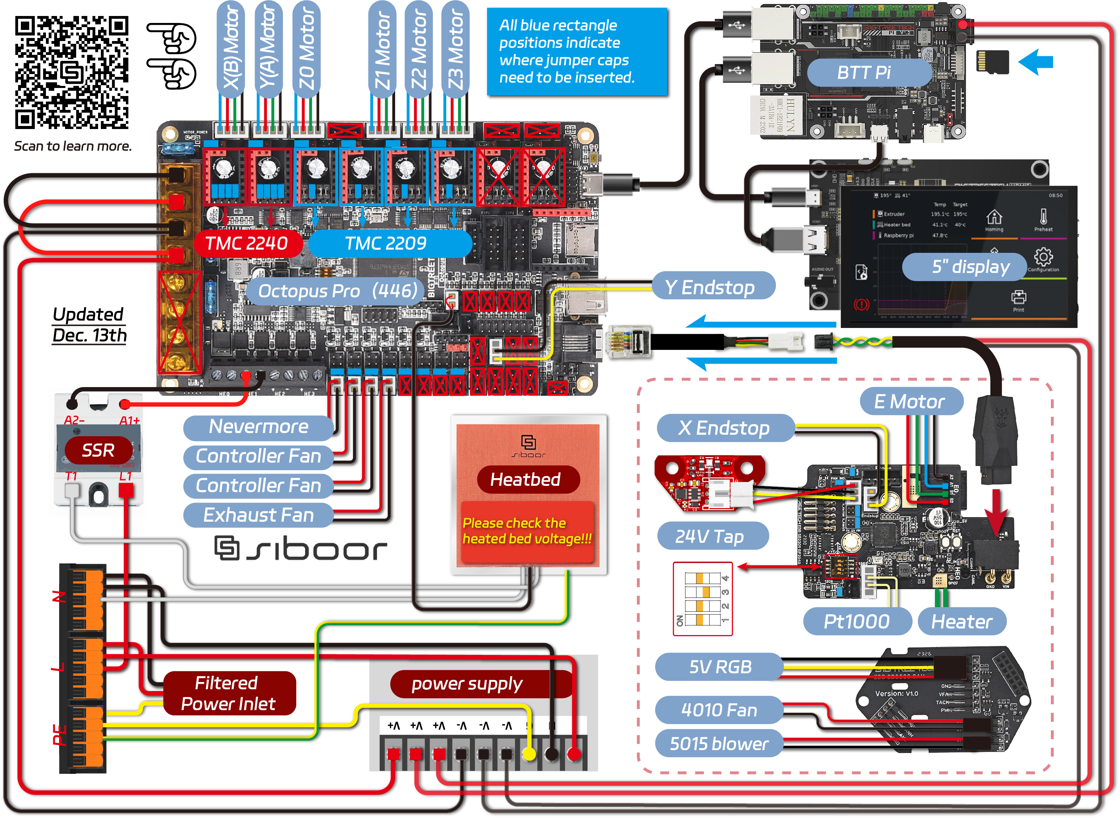
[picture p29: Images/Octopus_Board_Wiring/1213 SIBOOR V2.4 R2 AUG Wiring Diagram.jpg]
  

- Versions cartographer 
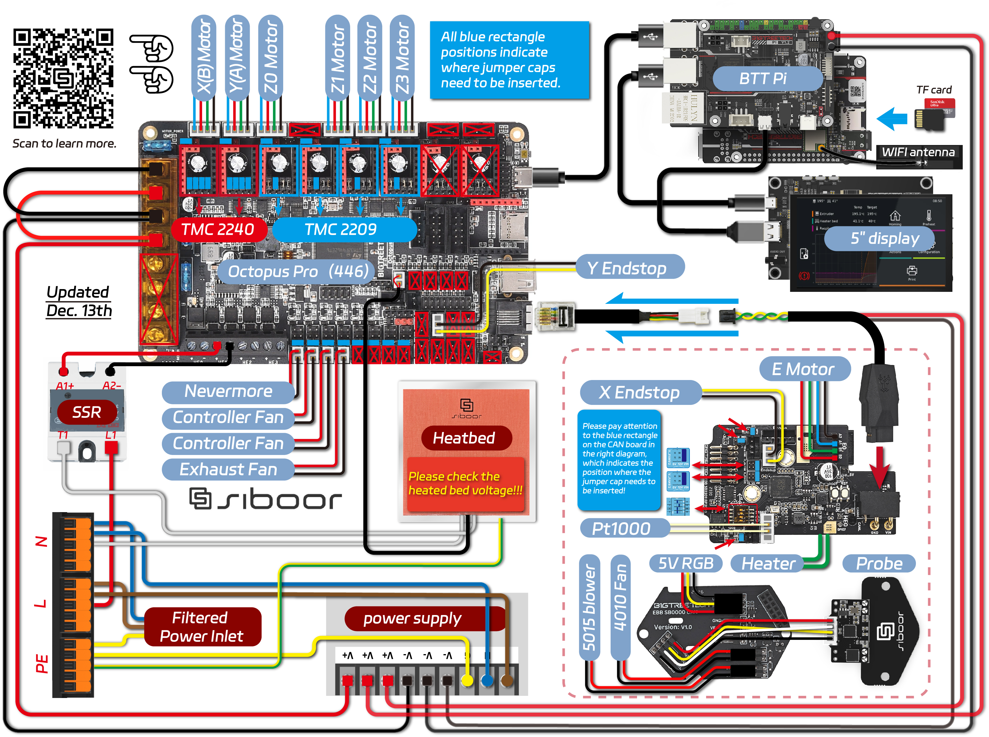
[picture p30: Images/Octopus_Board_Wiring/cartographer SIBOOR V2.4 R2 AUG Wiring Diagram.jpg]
  

## Version Update Notice: Board Output Adjustment

In this version, a significant upgrade has been implemented by successfully adjusting the board output from `BED_OUT` to `HE1`. This change aims to further optimize system performance.

### Debugging Consideration: Bed Heating Issues

If you encounter difficulties with bed heating during debugging, carefully inspect the `printer.cfg` file for bed configuration. Ensure that the bed heating pin is correctly set to `PA3`. Here is an example of the relevant configuration:

```yaml
[heater_bed]
heater_pin: PA3              # (BE0)
``` 

### The official VORON assembly manual, pages 174-209 are skipped in their entirety, and you are directed to a separate PDF created by SIBOOR.  
  [SIBOOR V2.4 AUG Wiring Schematic.pdf](https://github.com/Lzhikai/SIBOOR-Voron-2.4-AUG/blob/main/Images/Octopus_Board_Wiring/SIBOOR%20V2.4%20AUG%20Wiring%20Schematic.pdf)) 

### 5. Nevermore Installation  

- [Nevermore V6 Assembly Manual.pdf](https://github.com/Lzhikai/SIBOOR-Voron-2.4-AUG/blob/main/Manual/Nevermore%20V6%EF%BC%88SIBOOR%EF%BC%89.pdf) 

### 6. Networking and Configuration  

### Connect to WiFi
   - Prior to powering on the device, it is absolutely crucial to meticulously verify all electrical connections, ensuring strict adherence to the instructions, with 
   particular emphasis on the correct polarity of the power supply. Neglecting this essential step may lead to irreversible and severe consequences, causing irreparable 
   damage to the electrical equipment. It is imperative to follow these instructions without compromise for the safety and proper functionality of the device.
   - Connect the power cord, turn on the switch, and wait for the display screen to light up.
   - Tap on the "Menu" on the display screen.
   - Click on "Network."
   - Locate your WiFi network and tap the button on the right.
   - Enter the password and click "Save."
   - After returning to the previous level, find the device's IP address in the upper right corner.
  
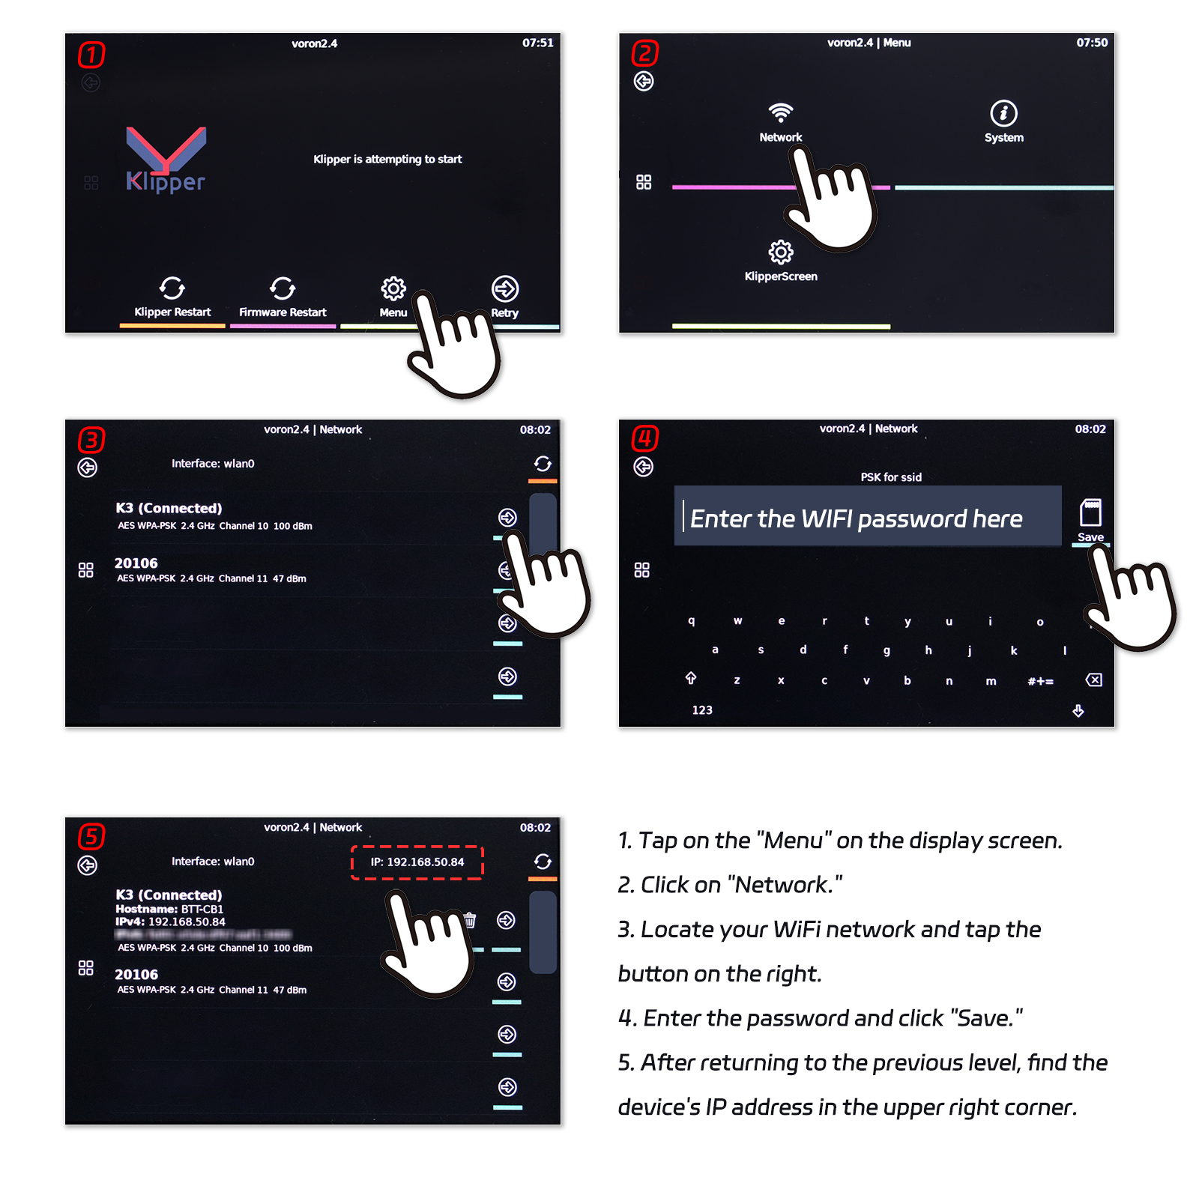
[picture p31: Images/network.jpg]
Network Image
   

   After obtaining the IP address of the device, you can enter the control page by typing the IP into the browser using a computer or cell phone in the same LAN. Before officially starting debugging, please continue reading.

### Log in to SSH
### SSH Tools PUTTY

Putty is a Windows SSH client with a long history. It is available as a free download [here](https://www.putty.org/).

To connect with Putty:

- Open Putty
- Enter your username and hostname in the “hostname” field, in the format `<user>@<host>`, for example, `biqu@BTT-CB1`,
- Certainly. You can also connect to the device directly using the IP address, for example: `pi@192.168.50.87`.  
- Press the “Open” button  

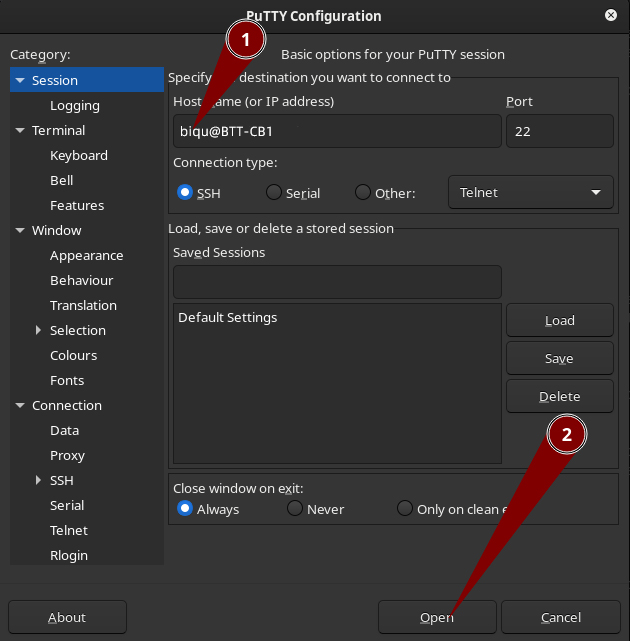
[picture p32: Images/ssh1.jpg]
Putty Image 1
   

- Since this is your first time connecting to this remote machine, you will encounter a security warning. It should be safe to just click accept.  

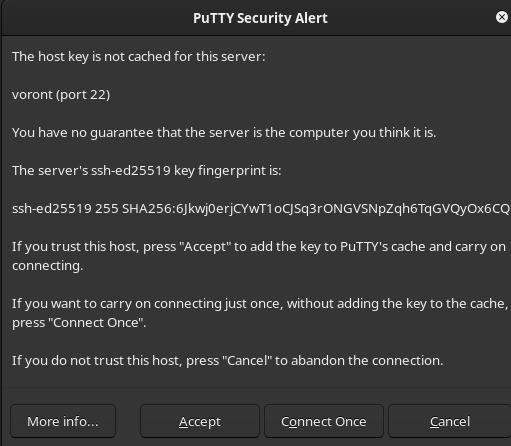
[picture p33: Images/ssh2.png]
Putty Image 2
   

### Putty Security Alert

- You will then find yourself with a black window and a password prompt. Type your password and press enter. It is normal for nothing to appear on the screen while you are typing the password.
- (Linux applications traditionally hide passwords completely rather than the more familiar dots or stars)  

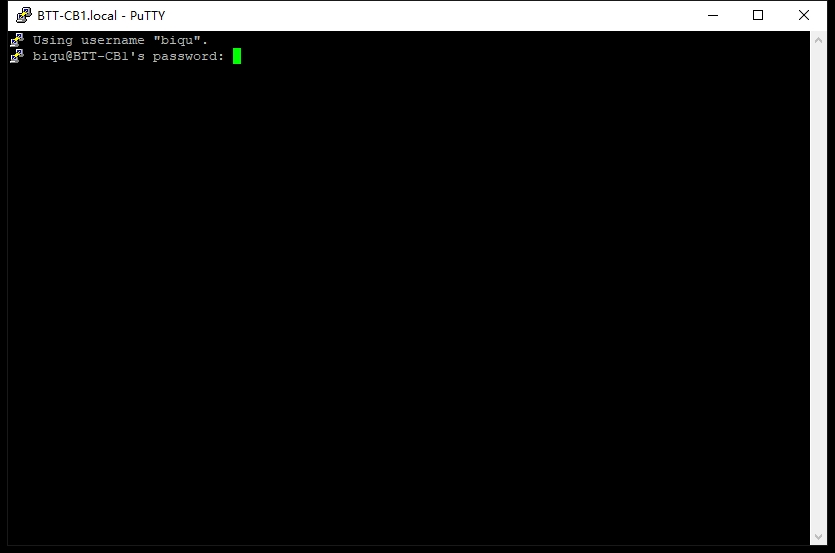
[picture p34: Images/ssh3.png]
Putty Image 3
   

*Note: Account and password are case-sensitive.*

### Connect the Octopus Pro Mainboard
   - To use the SSH tool to obtain the UUIDs and establish a connection with the OCTOPUS PRO mainboard and EBB 2209 CAN board, make sure to disconnect the cables between the EBB 2209 CAN board and the OCTOPUS PRO mainboard 
   before you begin. This will facilitate the differentiation of the UUIDs for these two boards.
   - Enter the following commands:
     ```bash
     cd ~/CanBoot/scripts
     python3 flash_can.py -i can0 -q
     ```  
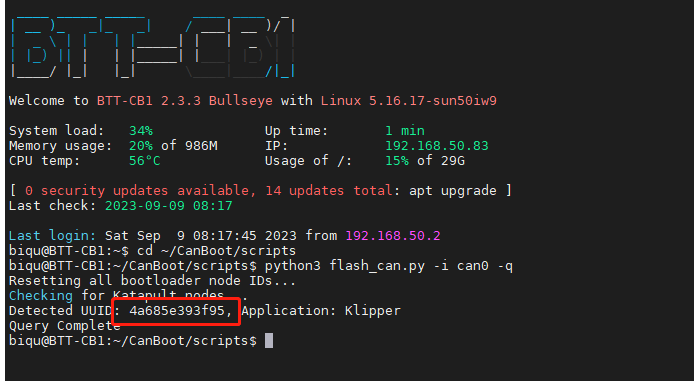
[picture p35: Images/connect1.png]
   <br/><br/>  
   
   - The displayed UUID is the mainboard's UUID. Copy and paste it into the corresponding location in the configuration file (cfg) document.

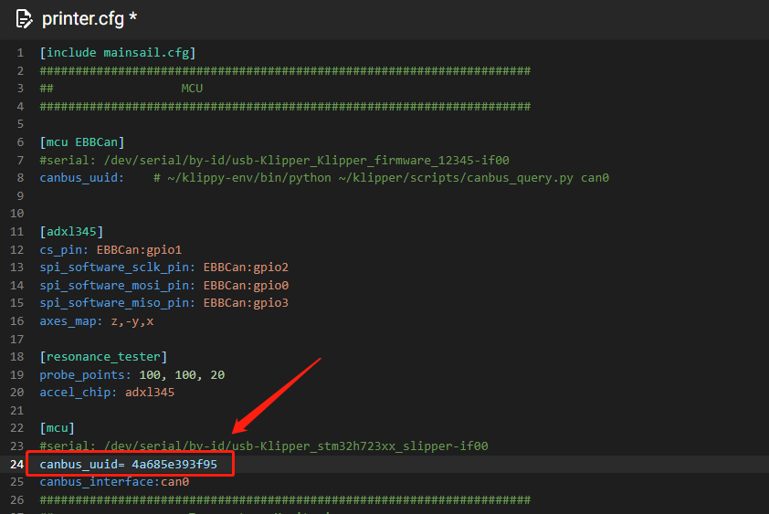
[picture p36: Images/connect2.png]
   <br/><br/> 

### Connect the EBB CAN Board  
   - Reinstall the cables that were just removed onto the OCTOPUS PRO mainboard. Next, let's proceed to read the UUID of the EBB 2209 CAN board.
   - Run the following command again:
     ```bash
     python3 flash_can.py -i can0 -q
     ```  
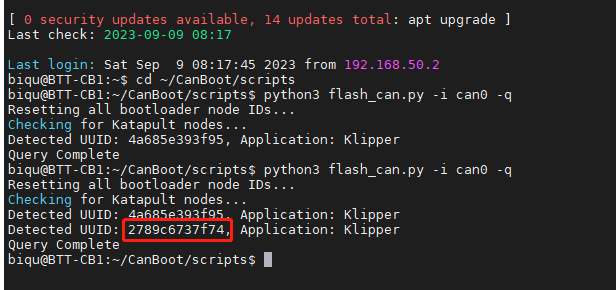
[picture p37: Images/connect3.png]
   <br/><br/>  
   
   - Obtain the UUID for the EBB CAN bus, copy it, and paste it into the corresponding location in the configuration file (cfg).  
   
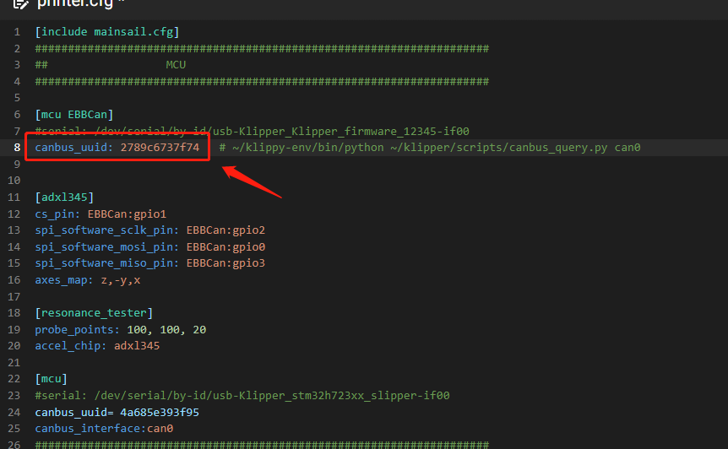
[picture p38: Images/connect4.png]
   <br/><br/> 
   
   - Click Save and restart to complete the device connection.

   <br/><br/>

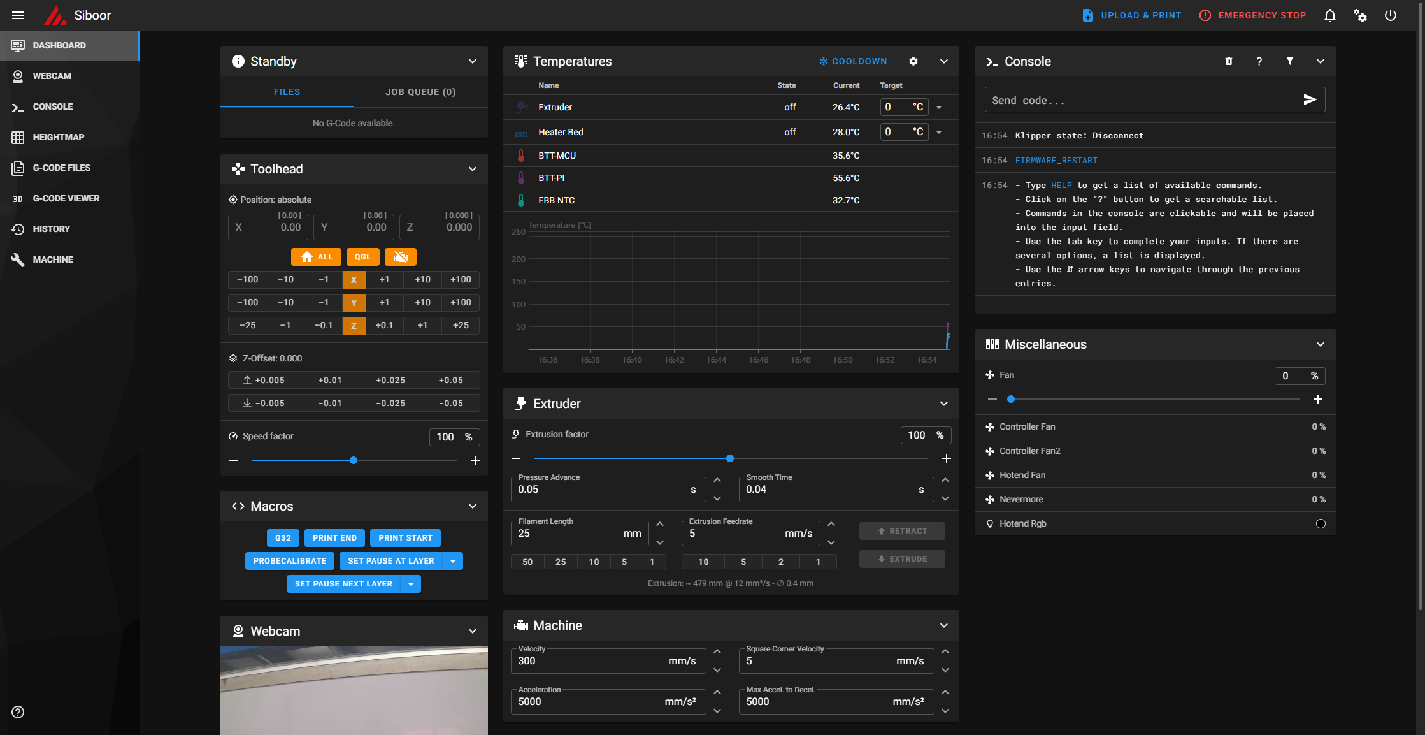
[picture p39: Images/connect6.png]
   <br/><br/>  

### Congratulations on reaching this point! You've done an excellent job. With the hardware assembly now complete, the next step involves device debugging. This is a phase that requires patience and a bit of learning. We recommend returning to the community for guidance on the upcoming steps.
   - https://docs.vorondesign.com/build/startup/

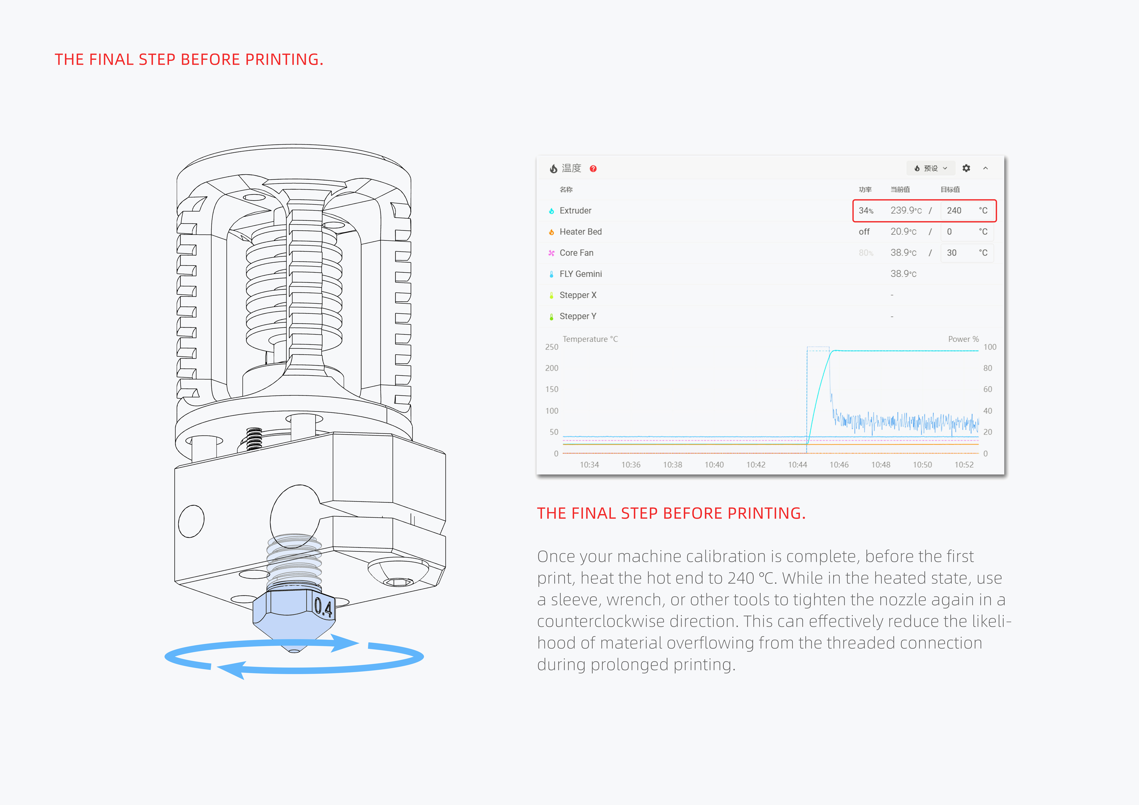
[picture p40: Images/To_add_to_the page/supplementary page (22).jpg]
   - 

## FAQ

- Where can I find the BOM list for SIBOOR V2.4 [AUG] to verify my package?  
  [Access the BOM list for SIBOOR V2.4 [AUG]](https://github.com/Lzhikai/SIBOOR-Voron-2.4-AUG/blob/main/SIBOOR_V2.4_AUG_BOM.md)).

- Is it necessary to burn the system and firmware?  
  The Pi's built-in system is pre-matched with the mainboard and CAN bus. Avoid version upgrades unless issues arise. 

- Why are some metal structural components unused?  
  Certain parts are designed for the Afterburner version and are not applicable here. Remove them before assembly.  

  <br/><br/>  

- Why are some screws in different positions from the official instructions?  
  Due to metal processing and weight reduction, some screws differ. See red annotations in Assembly_Manual_2.4r2.

- What are the Klipper account credentials?  
  Username: biqu, Password: biqu (Note: Case-sensitive)

- Why can't my Dragon hotend be installed on the printed part?  
  Remove the cylindrical joint on top of the Dragon hotend before installation. See illustration below.

- Why is there only one drag chain in my kit?  
  SIBOOR V2.4 [AUG] uses a CAN board, eliminating the need for X and Y axis drag chains. Wires will hang inside the chamber, reducing wear and poor contacts.

- Why can't my Z-axis reach the top due to the length limit of the Z-axis drag chain?  
  Removing the X and Y axis drag chains increases visible space, but printing height is still limited. For example, the 300 model can print up to around 280mm, and the 350 model up to around 330mm.

- Why are there no honeycomb skirts and fixed box panels in the kit?  
  If you didn't purchase decorative parts separately, you need to 3D print them.  [Download here](https://github.com/Lzhikai/SIBOOR-Voron-2.4-AUG/tree/main/STLs/Decorative%20print%20stl).

- Why are the motor wires for the X-axis and Y-axis not long enough?  
  This brand of motor has a standard wire length of one meter and requires the use of the red cable and JST terminal extension included in the kit. (X) B motor is recommended to be extended to 2 meters, and Y (A) 
  motor is recommended to be extended to 1.5 meters.

- Why does the hotend lower to 150℃ before raising to the printing temperature during pre-print preparation?  
  This is to prevent damage to the print bed in the event that the hot end heats up to high temperatures.

- Where can I download the system if mine is damaged?  
  [System](https://drive.google.com/file/d/1oGNcbJPUD5zyJWyPYAsPpvsBOQSKj1cR/view?usp=sharing) 

## Links
- VORON Official Website: [https://vorondesign.com/](https://vorondesign.com/)
- Klipper Official: [https://www.klipper3d.org/](https://www.klipper3d.org/)
- BTT Official: [https://github.com/bigtreetech](https://github.com/bigtreetech)

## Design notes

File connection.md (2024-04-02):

# SIBOOR-Voron-2.4-AUG
## [Octopus Pro(446)](https://github.com/bigtreetech/BIGTREETECH-OCTOPUS-Pro)+[BTT Pi](https://github.com/bigtreetech/BTT-Pi) + [CAN RP2040](https://github.com/bigtreetech/EBB/tree/master/EBB%20SB2209%20CAN%20(RP2040))  

## SSH
    login as: biqu
    password: biqu  
## OS image
* The latest system image is [here](https://github.com/Lzhikai/SIBOOR-Voron-2.4-AUG/releases). （The TF card included in the kit has already burned the system, and there is no need to burn it again. This is to prevent system damage from being used in the future.）
## WIFI Settings
* After the OS writes to the SD card, there is a FAT32 partition named `BOOT`, open `system.cfg` file with `Notpad`, `Notpad++` or `VSCode`.
<br/><br/>
* Set `WIFI_SSID` as your actual wifi name and `WIFI_PASSWD` as your actual wifi password, The space character can be parsed normally without additional escape character.<br/>
<br/><br/>  

* Then power on the btt pi, go to the backend of your router, look for a device named `BTT-CB1`, remember this IP address,  
and use tools such as `putty` or `MobaXterm`.  

* Make ssh connection

## Connect the motherboard and EBB    
* Connect the motherboard to the Pi using a USB cable
    * Connect via ssh and enter the following command    
```cd ~/CanBoot/scripts```    
```python3 flash_can.py -i can0 -q```

<br/><img src=https://github.com/Lzhikai/SIBOOR-Voron-2.4-AUG/blob/main/Images/connect1.png width="800"/><br/>    

* The UUID displayed at this time is the UUID of the motherboard canbus.     
    * Copy it and paste it into our cfg document.
  
<br/><img src=https://github.com/Lzhikai/SIBOOR-Voron-2.4-AUG/blob/main/Images/connect2.png width="800"/><br/>    

* Then connect to EBB canbus and enter this command again
    * Use RJ11 adapter to connect, pay attention to the position of green and yellow.
    * <br/><img src=https://github.com/Lzhikai/SIBOOR-Voron-2.4-AUG/blob/main/Images/toRJ11.jpg width="600"/><br/>
    * <br/><img src=https://github.com/Lzhikai/SIBOOR-Voron-2.4-AUG/blob/main/Images/RJ11.jpg width="600"/><br/>
    * It should be noted that the EBB canbus needs to be shorted to 120R, otherwise it cannot be connected.
    * <br/><img src=https://github.com/Lzhikai/SIBOOR-Voron-2.4-AUG/blob/main/Images/120R.png width="600"/><br/>   
    * ```python3 flash_can.py -i can0 -q```

<br/><img src=https://github.com/Lzhikai/SIBOOR-Voron-2.4-AUG/blob/main/Images/connect3.png width="800"/><br/>  

* This is the UUID of EBB canbus, Copy it and paste it here.

<br/><img src=https://github.com/Lzhikai/SIBOOR-Voron-2.4-AUG/blob/main/Images/connect4.png width="800"/><br/>    

* Then press this button, save and restart, and the device connection is completed.

<br/><img src=https://github.com/Lzhikai/SIBOOR-Voron-2.4-AUG/blob/main/Images/connect5.png width="800"/><br/>  
<br/><img src=https://github.com/Lzhikai/SIBOOR-Voron-2.4-AUG/blob/main/Images/connect6.png width="800"/><br/>

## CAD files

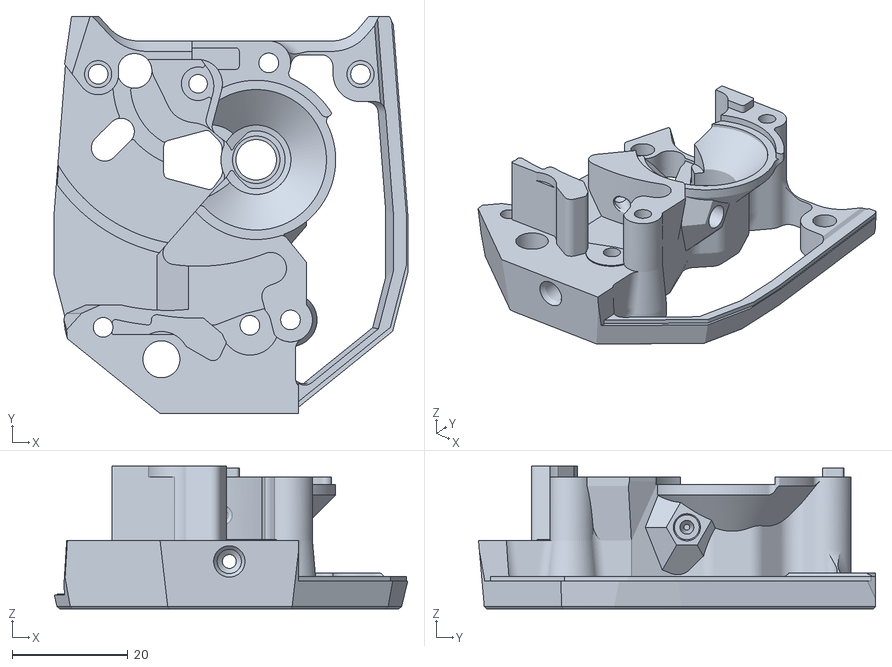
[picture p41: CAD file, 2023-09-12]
STLs/SB_hotend-[dragon_hotend]/main_body_EBB_SB.stl
61.2 x 68.7 x 24.7

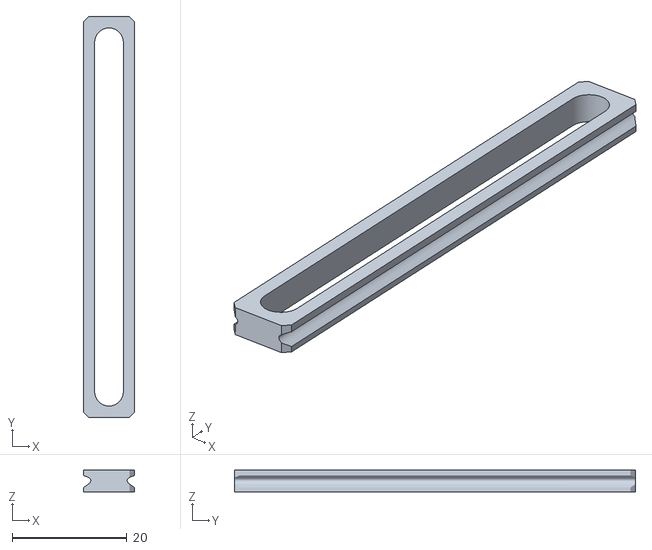
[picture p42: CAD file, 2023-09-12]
STLs/TAP_RC8/MGN9_Assembly_Tool.stl
8.90 x 70.0 x 3.80

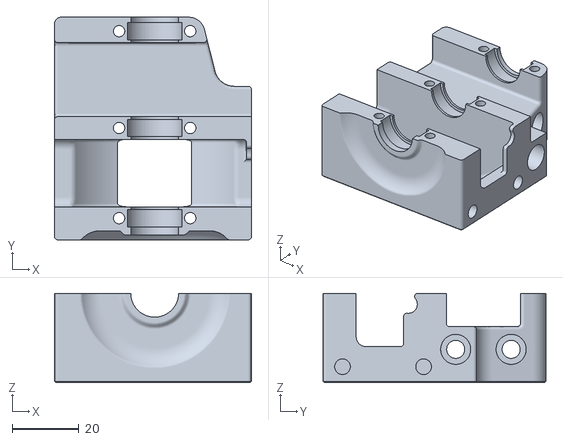
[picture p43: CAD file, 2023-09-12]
STLs/Regular color-[default_black]/z_drive_main_a_x2.stl
59.0 x 66.7 x 26.8

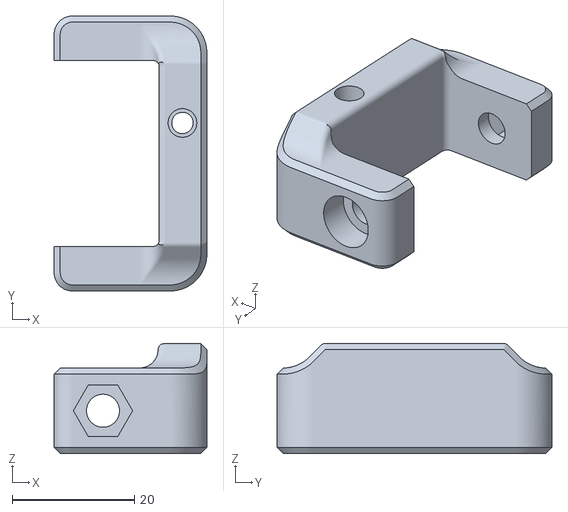
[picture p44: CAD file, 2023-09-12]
STLs/Accent color-[default_red]/[a]_tensioner_right.stl
25.0 x 45.0 x 18.0

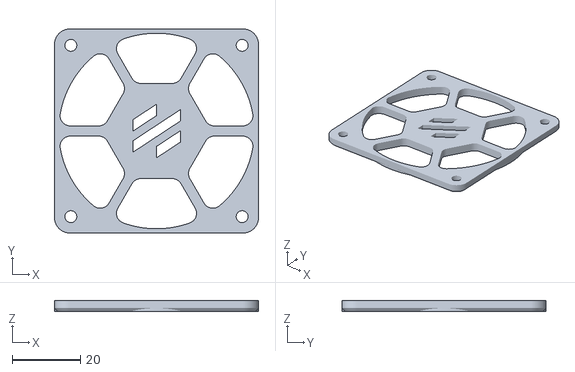
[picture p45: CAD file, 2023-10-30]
STLs/Decorative print stl/Exhaust_Filter/[a]_exhaust_fan_grill.stl
60.0 x 60.0 x 3.20

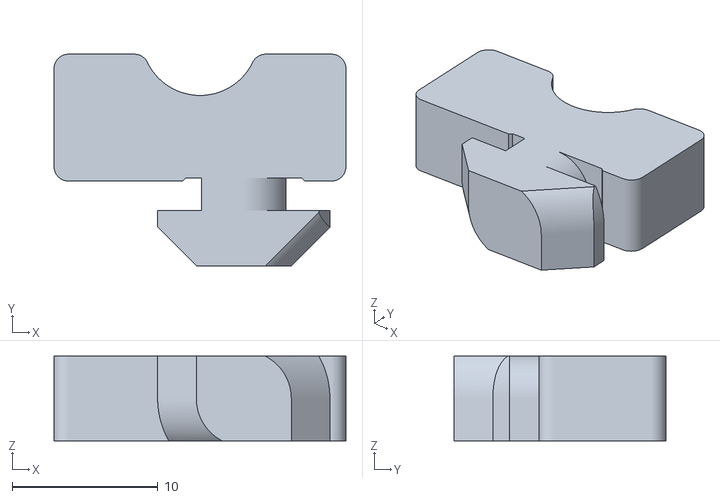
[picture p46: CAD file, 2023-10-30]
STLs/Decorative print stl/Panel_Mounting/deck_support_3mm_x8.stl
20.0 x 14.5 x 5.80

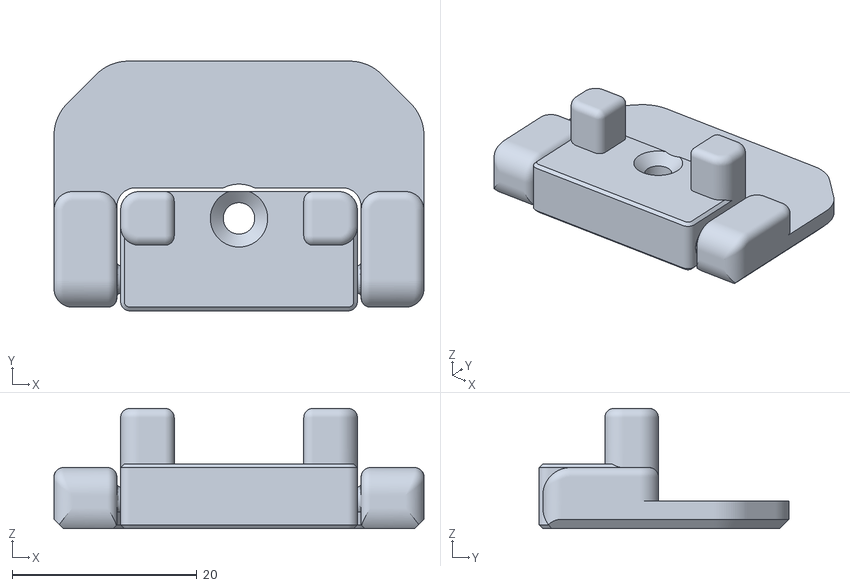
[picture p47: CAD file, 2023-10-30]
STLs/Decorative print stl/Panel_Mounting/Front_Doors/door_hinge_x6.stl
40.0 x 27.0 x 13.0

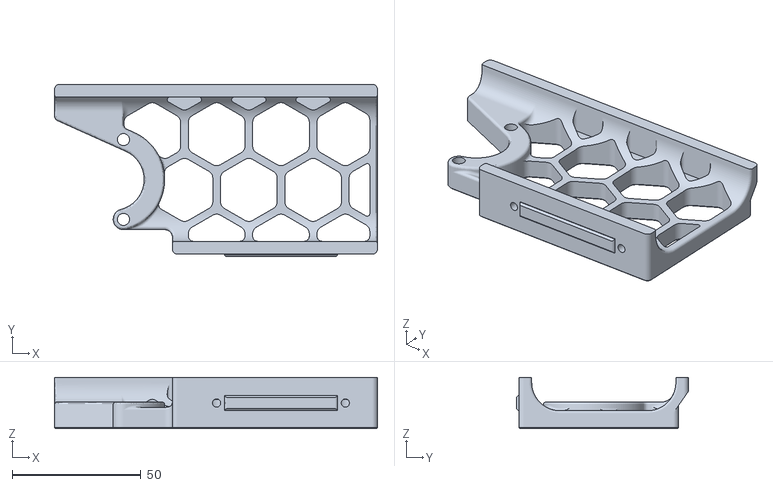
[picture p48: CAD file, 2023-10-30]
STLs/Decorative print stl/Skirts/300/front_skirt_b_300.stl
125.5 x 67.0 x 20.0

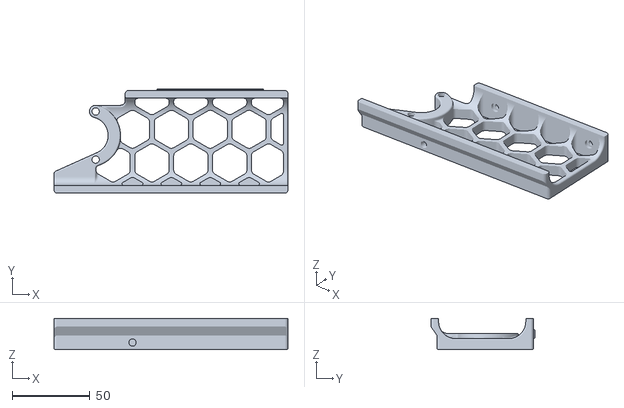
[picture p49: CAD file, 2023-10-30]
STLs/Decorative print stl/Skirts/350/front_skirt_a_350.stl
150.5 x 67.0 x 20.0

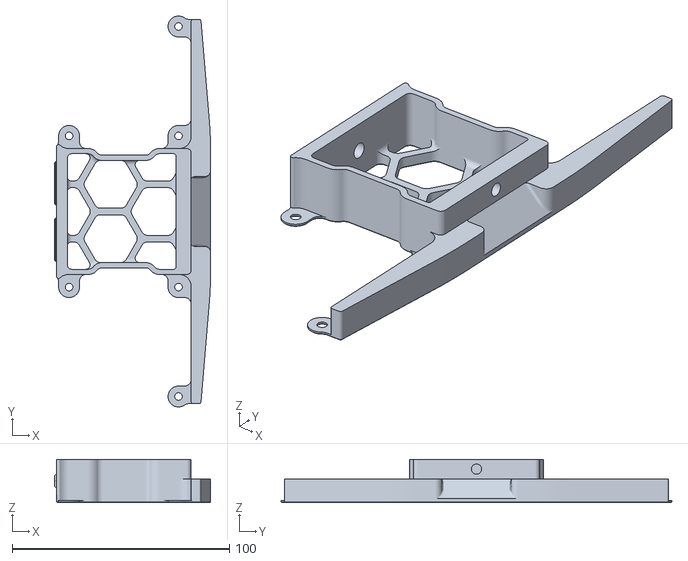
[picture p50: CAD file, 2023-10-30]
STLs/Decorative print stl/Skirts/side_fan_support_x2.stl
72.0 x 180.0 x 20.0

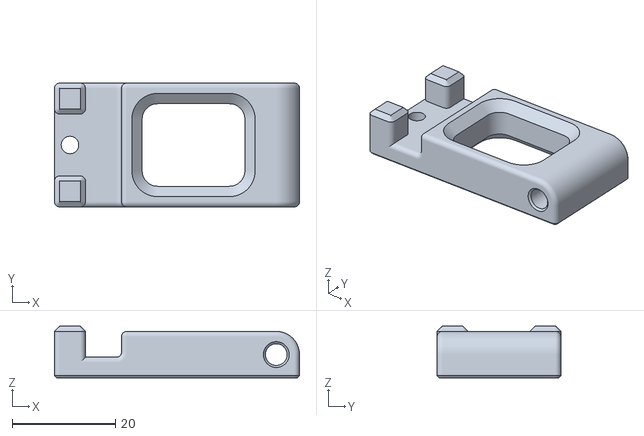
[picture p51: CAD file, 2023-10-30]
STLs/Decorative print stl/Spool_Management/bowden_retainer.stl
47.5 x 24.0 x 10.00

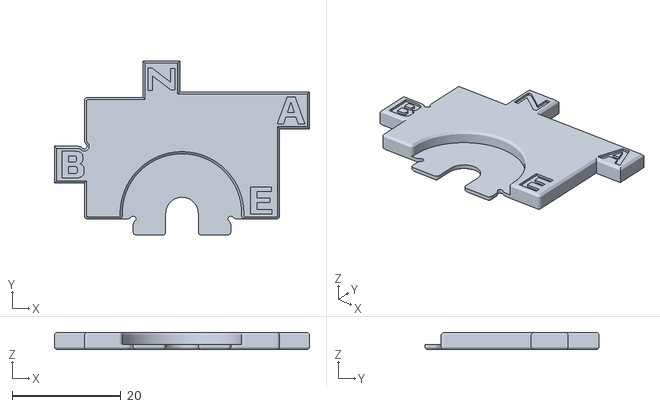
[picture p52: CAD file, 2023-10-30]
STLs/Decorative print stl/Tools/pulley_jig.stl
47.0 x 32.2 x 3.20

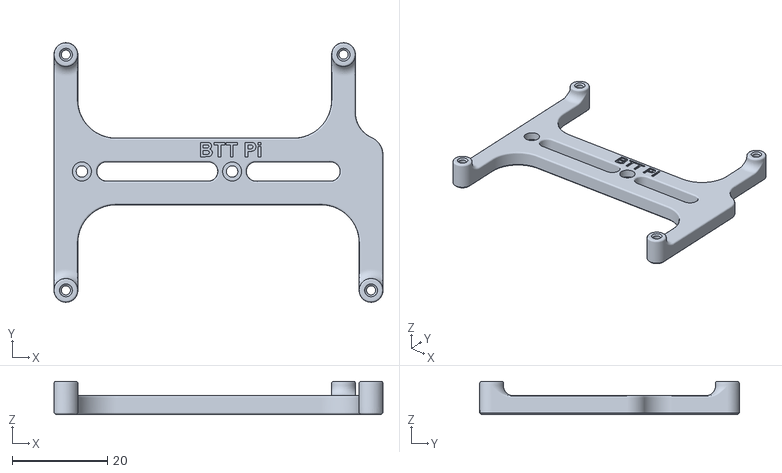
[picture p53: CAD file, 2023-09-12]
STLs/DIN/BTT PI.stl
69.0 x 54.4 x 7.00

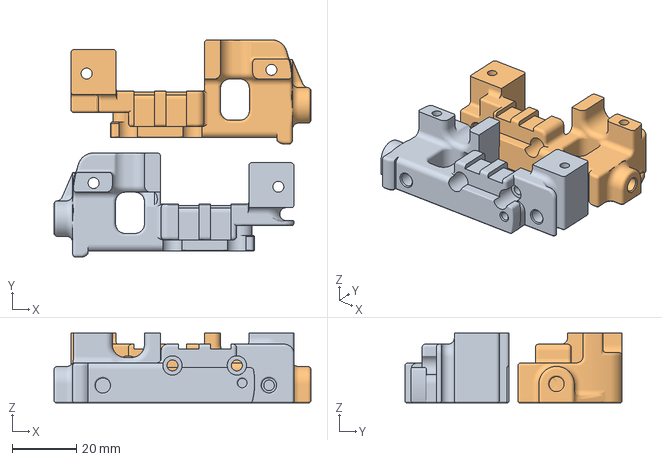
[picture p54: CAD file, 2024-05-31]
STLs/EDDY CW2 - 2mm back.3mf
79.8 x 67.6 x 21.6 mm

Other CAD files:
STLs/Regular color-[default_black]/z_drive_main_b_x2.stl
STLs/Nevermore V6/[Red] V6 filter box cover.stl
STLs/Regular color-[default_black]/HDMI V1.2 display.stl
STLs/SB_hotend-[dragon_hotend]/stealthburner_printhead_dragon_front.stl
STLs/Accent color-[default_red]/[a]_belt_tensioner_a_x2.stl
STLs/Accent color-[default_red]/[a]_belt_tensioner_b_x2.stl
STLs/Accent color-[default_red]/[a]_tensioner_left.stl
STLs/Accent color-[default_red]/[a]_z_belt_clip_lower_x4.stl
STLs/Accent color-[default_red]/[a]_z_belt_clip_upper_x4.stl
STLs/Accent color-[default_red]/[a]_z_drive_baseplate_a_x2.stl
STLs/Accent color-[default_red]/[a]_z_drive_baseplate_b_x2.stl
STLs/Accent color-[default_red]/[a]_z_tensioner_x4_9mm.stl
STLs/Accent color-[default_red]/拖链固定件×2.stl
STLs/DIN/MGN12_rail_guide_x2.stl
STLs/DIN/Octopus_bracket_set.stl
STLs/DIN/PSU_stabilizer_50mm.stl
STLs/DIN/lrs_200_psu_bracket_x2.stl
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

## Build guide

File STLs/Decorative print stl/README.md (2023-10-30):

# Decorative pieces that need to be printed by oneself

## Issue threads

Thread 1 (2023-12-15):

Wiring schematic  uncertainties/error

hartmanrik, 2023-12-15:
I would strongly suggest to look at pages 11 and 12 in your Wiring Guide: [https://github.com/Lzhikai/SIBOOR-Voron-2.4-AUG/blob/main/Images/Octopus_Board_Wiring/SIBOOR%20V2.4%20AUG%20Wiring%20Schematic.pdf](url)

They both show different wiring of L and N! It's a small error to make with big consequences!

notavisitor, 2023-12-15:
Thanks for the correction, it has been updated.

Closed 2023-12-15.

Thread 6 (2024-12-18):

Exhaust Fan

utrumo, 2024-12-18:
Hello. Please tell me how to test the exhaust fan and how to configure it?
Which port of the octopus board to connect it to is described in the instructions.
But it is not spelled out in the printer.cfg config, and there is nothing in the article initial startup checks about checking it.

utrumo, 2024-12-19:
I found pin name of this fan PD13 on this scheme
https://github.com/bigtreetech/BIGTREETECH-OCTOPUS-Pro/blob/master/Hardware/BIGTREETECH%20Octopus%20Pro%20V1.1-Pin.jpg

utrumo, 2024-12-19:
For orca slicer, according to the [instructions](https://github.com/SoftFever/OrcaSlicer/wiki/air-filtration), I corrected my printer.cfg:

Commented on these lines:
```
[fan]                                    # Parts Cooling Fan
pin: EBBCan:gpio13               # Fan pin
cycle_time: 0.00003                  # Cycle time
hardware_pwm: false              # hardware pwm
```

And below I added these:
```
#--------------------------------------------------------------------

# instead of using [fan], we define the default part cooling fan with [fan_generic] here
# this is the default part cooling fan
[fan_generic fan0]                   # Parts Cooling Fan
pin: EBBCan:gpio13                   # Fan pin
cycle_time: 0.00003                  # Cycle time
hardware_pwm: false

#--------------------------------------------------------------------

# this is the exhaust fan
[fan_generic fan3]
pin: PD13
cycle_time: 0.00003
hardware_pwm: false

#--------------------------------------------------------------------

[gcode_macro M106]
gcode:
    {% set fan = 'fan' + (params.P|int if params.P is defined else 0)|string %}
    {% set speed = (params.S|float / 255 if params.S is defined else 1.0) %}
    SET_FAN_SPEED FAN={fan} SPEED={speed}
```

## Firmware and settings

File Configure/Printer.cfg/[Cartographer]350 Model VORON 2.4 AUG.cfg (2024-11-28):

[include mainsail.cfg]

#####################################################################
##                   Model and Acceleration
#####################################################################

[printer]
kinematics: corexy                       # Printer type: corexy.
max_velocity: 300                        # Maximum speed (max. 300 mm/s).
max_accel: 5000                          # Maximum acceleration (max. 5000 mm/s²).
max_accel_to_decel: 8000                 # Maximum acceleration to deceleration (max. 8000 mm/s²).
max_z_velocity: 15                       # Z-axis maximum speed (15 mm/s).
max_z_accel: 350                         # Z-axis maximum acceleration (350 mm/s²).
square_corner_velocity: 5.0              # Square corner velocity (5.0 mm/s).

#####################################################################
##                      MCU EBBCan
#####################################################################

[mcu EBBCan]
canbus_uuid: 7f4959a3c4f6                # CAN bus unique identifier for EBBCan MCU.
#  The following command is used to view the ID of canbus and needs to be entered in the SSH terminal.
#  “~/klippy-env/bin/python ~/klipper/scripts/canbus_query.py can0”
#--------------------------------------------------------------
#  [adxl345]
#  cs_pin: EBBCan:gpio1                     # Chip select pin for ADXL345 accelerometer.
#  spi_software_sclk_pin: EBBCan:gpio2      # Software SPI clock pin.
#  spi_software_mosi_pin: EBBCan:gpio0      # Software SPI MOSI (Master Out Slave In) pin.
#  spi_software_miso_pin: EBBCan:gpio3      # Software SPI MISO (Master In Slave Out) pin.
#  axes_map: z,-y,x                         # Map the axes to match the printer's coordinate system.

#  [resonance_tester]
#  probe_points: 175, 175, 20               # Probe points for resonance testing.
#  accel_chip: adxl345                      # Accelerometer chip type used for resonance testing.

#####################################################################
##                     cartographer V3 (ADXL 345)
#####################################################################

[scanner]
canbus_uuid:
#    Fill in the UUID that was just recorded           
x_offset: 0                          
#    adjust for your cartographers offset from nozzle to middle of coil
y_offset: 21                         
#    adjust for your cartographers offset from nozzle to middle of coil
backlash_comp: 0.5
#   Backlash compensation distance for removing Z backlash before measuring
#   the sensor response.
# 
#   Offsets are measured from the centre of your coil, to the tip of your nozzle 
#   on a level axis. It is vital that this is accurate. 
calibration_method: touch
#    leave this as touch unless you want to use scan only for everything. 
sensor: cartographer
#    this must be set as cartographer unless using IDM etc.
sensor_alt: carto
#    alternate name to call commands. CARTO_TOUCH etc
scanner_touch_z_offset: 0.05         
#    This is the default and will be overwritten and added to the DO NOT SAVE area by using UI to save z offset
mesh_runs: 2
#    Number of passes to make during mesh scan.


[adxl345]
cs_pin: scanner:PA3
spi_bus: spi1

[resonance_tester]
accel_chip: adxl345             # Specifies ADXL345 accelerometer for resonance testing
probe_points:
    175, 175, 20                # Coordinates of the probe points for resonance testing

[safe_z_home]
home_xy_position: 175,175                # Example home_xy_position: 175,175 - This would be for a 350 * 350mm bed. 
z_hop: 10                                # Z axis hop height after homing.

#####################################################################
##                      MCU Octopus
#####################################################################

[mcu]
canbus_uuid: 319319024e88                # CAN bus unique identifier for Octopus MCU.
canbus_interface: can0                   # CAN bus interface.

#####################################################################
##                  Temperature Monitoring
#####################################################################

[temperature_sensor EBB_NTC]
sensor_type: Generic 3950                # Sensor type for NTC thermistor (commented out).
sensor_pin: EBBCan:gpio28                # Pin connected to NTC thermistor (commented out).

[temperature_sensor BTT-MCU]
sensor_type: temperature_mcu             # MCU internal temperature sensor.

[temperature_sensor BTT-PI]
sensor_type: temperature_host            # Host system internal temperature sensor.

#####################################################################
#                        B(X) ---------A(Y)
#                        |                |
#                        |                |
#                        |--------E-------|
#                        |                |
#                        |                |
#                        |                |
#####################################################################
##                   X-axis on MOTOR_0(B Motor)
#####################################################################

[stepper_x]
step_pin: PF13                           # X-axis motor pulse pin setting
dir_pin: !PF12                           # X-axis motor direction pin setting
enable_pin: !PF14                        # X-axis motor enable pin setting
microsteps: 32                           # Motor microsteps setting
rotation_distance: 40                    # Active pulley circumference in mm (2GT-20T pulley 40, 2GT-16T pulley 32)
full_steps_per_rotation: 200             # Number of pulses required for a single motor revolution (1.8 degree motor: 200, 0.9 degree motor: 400)
endstop_pin: EBBCan:gpio24               #PG6 # Limit switch pin setting (X-)
position_min: 0                          # X-axis minimum travel - software limit
position_endstop: 350                    # Mechanical reset point coordinates for X-axis (change to 350 for 350 models)
position_max: 350                        # X-axis maximum travel - software limit (change to 350 for 350 models)
homing_speed: 200                        # Reset speed - maximum 100
homing_retract_dist: 5                   # Setback distance after the first trigger of the reset switch
homing_positive_dir: true                # Direction of reset (generally no change required)

[tmc2240 stepper_x]
cs_pin: PC4                              # Chip select pin for TMC2240 driver
spi_software_sclk_pin: PA5               # SPI software clock pin
spi_software_mosi_pin: PA7               # SPI software MOSI pin
spi_software_miso_pin: PA6               # SPI software MISO pin
driver_TPFD: 0                           # TMC2240 TPFD setting
run_current: 1.2                         # Motor running current value (A)

#####################################################################
##                   Y-axis on MOTOR_1（A Motor）
#####################################################################

[stepper_y]
step_pin: PG0                            # Y-axis motor pulse pin setting
dir_pin: !PG1                            # Y-axis motor direction pin setting
enable_pin: !PF15                        # Y-axis motor enable pin setting
microsteps: 32                           # Motor microsteps setting
rotation_distance: 40                    # Active pulley circumference in mm (2GT-20T pulley 40, 2GT-16T pulley 32)
full_steps_per_rotation: 200             # Number of pulses required for a single motor revolution (1.8 degree motor: 200, 0.9 degree motor: 400)
endstop_pin: PG9                         # Limit switch pin setting (Y-)
position_min: 0                          # Y-axis minimum travel - software limit
position_endstop: 350                    # Mechanical reset point coordinates for Y-axis (change to 350 for 350 models)
position_max: 350                        # Y-axis maximum travel - software limit (change to 350 for 350 models)
homing_speed: 200                        # Reset speed - maximum 100
homing_retract_dist: 5                   # Setback distance after the first trigger of the reset switch
homing_positive_dir: true                # Direction of reset (generally no change required)

[tmc2240 stepper_y]
cs_pin: PD11                             # Chip select pin for TMC2240 driver
spi_software_sclk_pin: PA5               # SPI software clock pin
spi_software_mosi_pin: PA7               # SPI software MOSI pin
spi_software_miso_pin: PA6               # SPI software MISO pin
driver_TPFD: 0                           # TMC2240 TPFD setting
run_current: 1.2                         # Motor running current value (A)
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

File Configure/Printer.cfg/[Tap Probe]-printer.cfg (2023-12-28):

[include mainsail.cfg]
#####################################################################
## 	                MCU
#####################################################################

[mcu EBBCan]
#serial: /dev/serial/by-id/usb-Klipper_Klipper_firmware_12345-if00
canbus_uuid: 2789c6737f74   
#  The following command is used to view the ID of canbus and needs to be entered in the ssh terminal.
# “ ~/klippy-env/bin/python ~/klipper/scripts/canbus_query.py can0 ”

#--------------------------------------------------------------
[adxl345]
cs_pin: EBBCan:gpio1
spi_software_sclk_pin: EBBCan:gpio2
spi_software_mosi_pin: EBBCan:gpio0
spi_software_miso_pin: EBBCan:gpio3
axes_map: z,-y,x

[resonance_tester]
probe_points: 100, 100, 20
accel_chip: adxl345

[mcu]
#serial: /dev/serial/by-id/usb-Klipper_stm32h723xx_slipper-if00
#--------------------------------------------------------------
# Query the ID of canbus：
# cd ~/CanBoot/scripts
# python3 flash_can.py -i can0 -q
canbus_uuid= 4a685e393f95     
canbus_interface:can0
#####################################################################
##	                 Temperature Monitoring
#####################################################################
[temperature_sensor EBB_NTC]
sensor_type: Generic 3950
sensor_pin: EBBCan:gpio28
[temperature_sensor BTT-MCU]        
sensor_type: temperature_mcu
[temperature_sensor BTT-PI]
sensor_type: temperature_host

#####################################################################
##                     Model and acceleration
#####################################################################
[printer]
kinematics: corexy           # Printer type：corexy
max_velocity: 300            # Maximum speed (max. 300)
max_accel: 5000              # Maximum acceleration (max. 4000)
max_accel_to_decel: 5000     # Maximum acceleration to deceleration (max. 4000)
max_z_velocity: 15           # Z-axis maximum speed
max_z_accel: 350             # Z-axis maximum acceleration
square_corner_velocity: 5.0  # Square corner speed

#####################################################################
#   B(X) ---------A(Y)
#   |                |
#   |--------E-------|
#   |                |
#   |                |
#   |                |
#####################################################################
##                   X-axis on MOTOR_0(B Motor)
#####################################################################

[stepper_x]
step_pin: PF13             # X-axis motor pulse pin setting
dir_pin: PF12              # X-axis motor direction pin setting
enable_pin: !PF14          # X-axis motor enable pin setting
microsteps: 32             # Motor microsteps Setting
rotation_distance: 40      # Active pulley circumference mm (2GT-20T pulley 40, 2GT-16T pulley 32)
full_steps_per_rotation:200   # Number of pulses required for a single motor revolution (1.8 degree motor: 200, 0.9 degree motor: 400)
endstop_pin: EBBCan:gpio24 #PG6           # Limit switch PIN pin setting（X-）
position_min: 0            # X-axis minimum travel - software limit
position_endstop: 300  #350    ## Mechanical reset point coordinates for X-axis (change to 350 for 350 models)
position_max: 300  #350       ## X-axis maximum travel - software limit (change to 350 for 350 models)
homing_speed: 50           # Reset speed maximum 100
homing_retract_dist: 5     # Setback distance after the first trigger of the reset switch
homing_positive_dir: true  # Direction of reset (generally no change required)

[tmc2240 stepper_x]
cs_pin: PC4
spi_software_sclk_pin: PA5
spi_software_mosi_pin: PA7
spi_software_miso_pin: PA6
driver_TPFD: 0
run_current: 0.85

#####################################################################
##                   Y-axis on MOTOR_1(A Motor)
#####################################################################

[stepper_y]
step_pin: PG0              # Y-axis motor pulse pin setting
dir_pin: PG1               # Y-axis motor direction pin setting
enable_pin: !PF15          # Y-axis motor enable pin setting
microsteps: 32             # Motor microsteps Setting
rotation_distance: 40      # Active pulley circumference mm (2GT-20T pulley 40, 2GT-16T pulley 32)
full_steps_per_rotation:200   # Number of pulses required for a single motor revolution (1.8 degree motor: 200, 0.9 degree motor: 400)
endstop_pin: PG9           # Limit switch PIN pin setting（Y-）
position_min: 0            # X-axis minimum travel - software limit
position_endstop: 300  #350      # Mechanical reset point coordinates for Y-axis (change to 350 for 350 models)
position_max: 300  #350          # Y-axis maximum travel - software limit (change to 350 for 350 models)
homing_speed: 50           # Reset speed maximum 100
homing_retract_dist: 5     # Setback distance after the first trigger of the reset switch
homing_positive_dir: true  # Direction of reset (generally no change required)

[tmc2240 stepper_y]
cs_pin: PD11
spi_software_sclk_pin: PA5
spi_software_mosi_pin: PA7
spi_software_miso_pin: PA6
driver_TPFD: 0
run_current: 0.85

####################################################################################
#   z1 -------------- z2
#   |                 |
#   |                 |
#   |                 |
#   |                 |
#  z0---   display ---z3
#####################################################################
##                  Z0-axis
#####################################################################
##		Z0-axis on MOTOR2_1(left front)
[stepper_z]
step_pin: PF11    		   # Z-axis motor pulse pin
dir_pin: !PG3               # Z-axis motor direction pin setting
enable_pin: !PG5           # Z-axis motor enable pin setting
rotation_distance: 40      # Active pulley circumference mm (2GT-20T pulley 40, 2GT-16T pulley 32)
gear_ratio: 80:16          # reduction ratio
microsteps: 16             # microsteps
endstop_pin: probe:z_virtual_endstop #PG10          # Limit switch interface
##  position_endstop is the distance of the Z limit pin trigger point from the print surface.
##  Positive value = above the termination point of the platform，
##  Negative value = termination point below the plateau.
##  Increasing the value of position_ endstop will bring the nozzle closer to the bed.
##  After running Z_ENDSTOP_CALIBRATE, position_endstop will be stored at the end of the CFG configuration.
##position_endstop: 0.5      # Modified as per actual
position_max: 280   #340       # Maximum Z-axis print height   350mm=340
position_min: -5           # Soft Limit Minimum Stroke
homing_speed: 10           # Reset speed - maximum 20
second_homing_speed: 3     # Secondary reset speed - maximum 10
homing_retract_dist: 3     # Retreat distance
#--------------------------------------------------------------------
[tmc2209 stepper_z]        # TMC2209
uart_pin: PC6              # drive communications port
interpolate: true          # Whether to enable 256 microstep interpolation
run_current: 0.8           # Motor running current value(mA)
hold_current: 0.8          # holding current(mA)
sense_resistor: 0.110      # Do not change the drive sampling resistor
stealthchop_threshold: 200 # Mute threshold

#--------------------------------------------------------------------#
##		Z1-axis on MOTOR3(left rear)
[stepper_z1]
step_pin: PG4              # Z1-axis motor pulse pin
dir_pin: PC1              # Z1-axis motor direction pin setting
enable_pin: !PA0           # Z1-axis motor enable pin setting
rotation_distance: 40      # Active pulley circumference mm (2GT-20T pulley 40, 2GT-16T pulley 32)
gear_ratio: 80:16          # reduction ratio
microsteps: 16             # microsteps
#--------------------------------------------------------------------
[tmc2209 stepper_z1]       # TMC2209
uart_pin: PC7              # drive communications port
interpolate: true          # Whether to enable 256 microstep interpolation
run_current: 0.8           # Motor running current value(mA)
hold_current: 0.8          # holding current(mA)
sense_resistor: 0.110      # Do not change the drive sampling resistor
stealthchop_threshold: 200 # Mute threshold
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

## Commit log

2023-09-19 wiring diagram
2023-09-21 Update SIBOOR V2.4 R2 AUG Wiring Diagram.jpg
2023-09-27 gear_ratio: 50:10
    [pro446.cfg]
2023-09-28 Update 0928 SIBOOR V2.4 R2 AUG Wiring Diagram.jpg
2023-10-24 300mm and 350mm
    [pro446.cfg]
2023-10-25 Restore print head temperature
    [pro446.cfg]
2023-10-30 Decorative print stl
    [Filament_Card.stl, Filament_Card_Caddy_25.stl, Heatset_Practice.stl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]
2023-11-20 Correct wiring diagram
2023-11-25 Create V2.4 R2 V1.5 CNC Assembly discrepant Manual.pdf
2023-12-09 update Assemble
2023-12-19 update Display assembly
2023-12-27 Update printer.cfg
    Changed Neopixel pin assign from PB10 to PB0 to match with Octopus Pro 1.0 (F446 model)
    [printer.cfg]
2024-04-02 cartographer wiring
2024-05-31 Create EDDY CW2 - 2mm back.3mf
    [EDDY CW2 - 2mm back.3mf]
2024-07-03 Update Wiring
2024-09-20 Create HDMI V1.2 display.stl
    [HDMI V1.2 display.stl]
2024-11-26 update cfg
    [[Cartographer]300 Model VORON 2.4 AUG.cfg, [Cartographer]350 Model VORON 2.4 AUG.cfg, [Tap Probe]-printer.cfg]
2024-11-28 Update [Cartographer]300 Model VORON 2.4 AUG.cfg
    [[Cartographer]300 Model VORON 2.4 AUG.cfg]
2024-11-28 Update [Cartographer]350 Model VORON 2.4 AUG.cfg
    [[Cartographer]350 Model VORON 2.4 AUG.cfg]
